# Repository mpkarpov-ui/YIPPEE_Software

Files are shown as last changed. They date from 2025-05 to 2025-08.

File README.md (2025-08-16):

# YIPPEE

**Your Integrated Presicion Positioning (and) Elevation Engine**

### About YIPPEE

YIPPEE is a personal project that I started in early 2025, and was my entry into hardware design, as I was interested in learning more about how my [college rocketry team](https://www.illinoisspacesociety.org/spaceshot) developed the hardware for its flight computers.

After receiving help from our Electronic Hardware lead, I had a schematic and layout I was happy with and produced it in our school's electronic lab. The software for this project was in majority written by me with some key contributions from [Surag Nuthulapaty](https://github.com/SuragNuthulapaty), who is a very smart and cool guy.

### Using YIPPEE

#### Hardware

All hardware schematics are present in `hardware/`. As of August 2025, the RPP diode is no longer being produced or sold, but can just be replaced with a jumper wire.

All components can be sourced commercially through Transfer Multisort Elektronik (TME), DigiKey, Mouser, LCSC, and Amazon.

All hardware schematics are free for use.

#### Software

YIPPEE software is compiled with [Platformio](https://platformio.org/), which offers easy VSCode integration with their extension. The configuration defines 4 targets which are described below:

**hardware_test** – This target suspends all normal functions of the flight computer and pre-empts them by putting in code configured to mass-test the components on the board, this is useful for board assembly and debugging.

**main** - This is the main "flight code" and includes finished drivers, flash memory management system, telemetry code, and a barometer-based flight FSM.

**mem_offload** – This target also pre-empts the main flight code, but instead of testing components, it allows offloading data off the flash memory chip.

**ground** (Feather M0) – Running on a commercial-off-the-shelf radio module (the Feather M0 RFM96), this code can receive YIPPEE radio signals and process them to display live board telemetry on the ground.

To start with your YIPPEE board, connect the USB port on the Teensy 4.0 to any COM port on your computer. Then flash the appropriate target through your Platformio interface of choice.

All YIPPEE software is free to reference.

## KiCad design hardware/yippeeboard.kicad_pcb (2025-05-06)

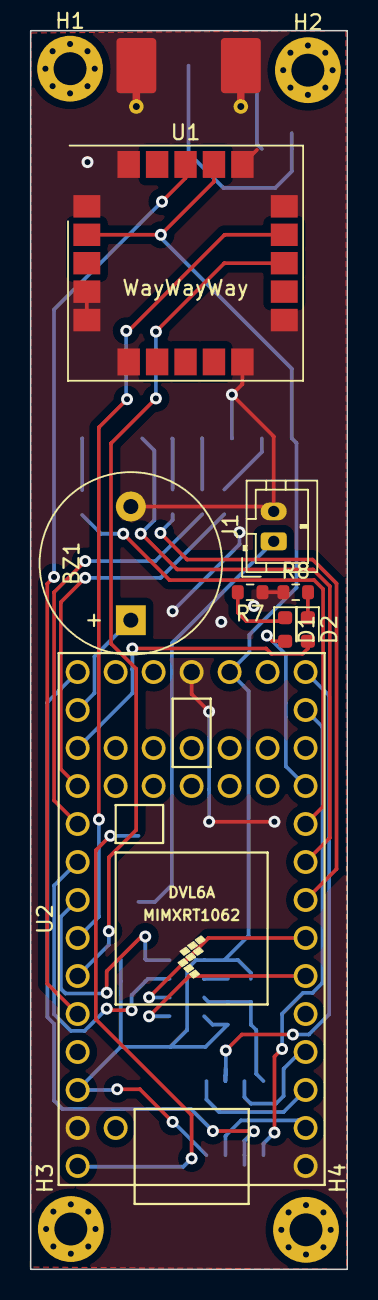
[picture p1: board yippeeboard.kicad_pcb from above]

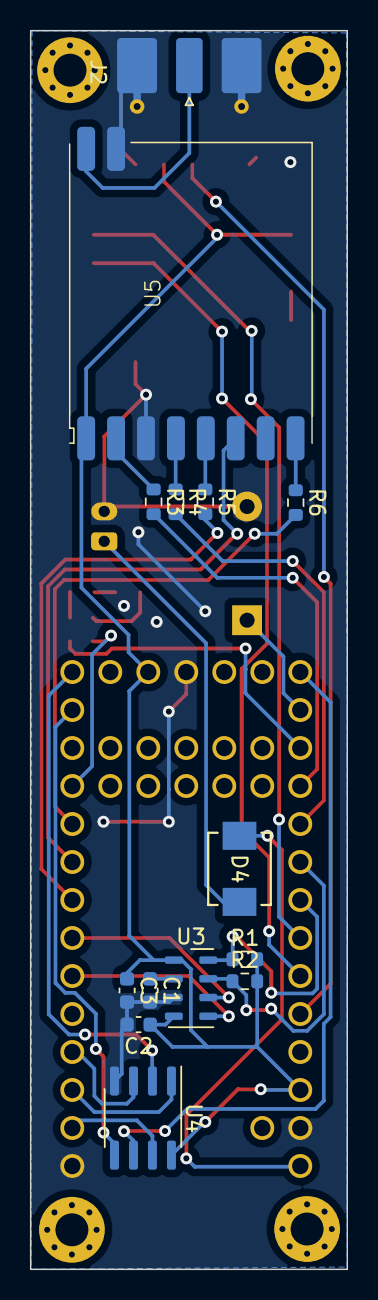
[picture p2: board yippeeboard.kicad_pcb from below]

Board: 2 copper layers, 21.2 x 82.8 mm, 26 parts (14 on the bottom side), 33 nets.

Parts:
BZ1: WST-1210; Buzzer_12x9.5RM7.6
C1, C3: 100 nF; C_0603_1608Metric
C2: 10 μF; C_0603_1608Metric
D1: LED_B; LED_0603_1608Metric
D2: LED_G; LED_0603_1608Metric
D4: LSM115JE3/TR13; DO-214BA_MCH
H1, H2, H3, H4: MountingHole_Pad; MountingHole_2.2mm_M2_Pad_Via
J1: Conn_01x02; JST_PH_B2B-PH-K_1x02_P2.00mm_Vertical
J2: Conn_Coaxial; SMA_Molex_73251-2120_EdgeMount_Horizontal
R1, R2: 4.7kΩ; R_0603_1608Metric
R3, R4, R5, R6: 22Ω; R_0603_1608Metric
R7, R8: 470; R_0603_1608Metric
U1: SAM-M10Q; ublox_SAM-M8Q
U2: Teensy4.0; Teensy40
U3: MPL3115A2; NXP_LGA-8_3x5mm_P1.25mm_H1.1mm
U4: SST26VF040A-104I/SN; SOIC-8_3.9x4.9mm_P1.27mm
U5: HM-TRLR-S-433; HM-TRLR-S-xxx

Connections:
+3V3: C2.1, C3.1, R1.2, R2.2, U1.2 (VCC_IO), U1.17 (VCC), U2.16 (3V3), U2.31 (3V3), U3.1 (VDD), U3.4 (VDDIO), U4.8 (VDD), U5.1 (VCC)
/BARO_INT1: U2.7 (5_IN2), U3.6 (INT1)
/BARO_INT2: U2.6 (4_BCLK2), U3.5 (INT2)
/BUZZER_SIG: BZ1.1 (-), U2.21 (14_A0_TX3_SPDIF_OUT)
/GPS_RESET: U1.18 (~RESET), U2.29 (22_A8_CTX1)
/GPS_RX: U1.13 (TXD), U2.28 (21_A7_RX5_BCLK1)
/GPS_TX: U1.14 (RXD), U2.27 (20_A6_TX5_LRCLK1)
/I2C_SCL: R1.1, U2.26 (19_A5_SCL0), U3.8 (SCL)
/I2C_SDA: R2.1, U2.25 (18_A4_SDA0), U3.7 (SDL)
/LED_B: D1.2 (A), U2.11 (9_OUT1C)
/LED_G: D2.2 (A), U2.22 (15_A1_RX3_SPDIF_IN)
/LORA_CONFIG: R5.2, U2.8 (6_OUT1D)
/LORA_RESET: R6.2, U2.10 (8_TX2_IN1)
/LORA_RX: R3.2, U2.23 (16_A2_RX4_SCL1)
/LORA_SLEEP: U2.9 (7_RX2_OUT1A), U5.6 (SLEEP)
/LORA_TX: R4.2, U2.24 (17_A3_TX4_SDA1)
/MEM_CS: U2.3 (1_TX1_CTX2_MISO1), U4.1 (~CE)
/MEM_HOLD: U2.2 (0_RX1_CRX2_CS1), U4.7 (~HOLD)
/MEM_WRITE_PROTECT: U2.4 (2_OUT2), U4.3 (~WP)
/PWR_VIN: D4.1 (K), U2.33 (VIN)
/SPI_MISO: U2.14 (12_MISO_MQSL), U4.2 (SO)
/SPI_MOSI: U2.13 (11_MOSI_CTX1), U4.5 (SI)
/SPI_SCK: U2.20 (13_SCK_CRX1_LED), U4.6 (SCK)
GND: BZ1.2 (+), C1.2, C2.2, C3.2, J1.2, J2.2 (Ext), R7.1, R8.1, U1.1 (GND), U1.4 (GND), U1.5 (GND), U1.6 (GND), U1.10 (GND), U1.11 (GND), U1.15 (GND), U1.16 (GND), U1.20 (GND), U2.1 (GND), U2.17 (GND), U2.32 (GND), U3.3 (GND), U4.4 (VSS), U5.3 (GND), U5.10 (GND)
unnamed: D1.1 (K), R7.2
unnamed: D2.1 (K), R8.2
unnamed: D4.2 (A), J1.1
unnamed: J2.1 (In), U5.9 (ANT)
unnamed: C1.1, U3.2 (CAP)
unnamed: R4.1, U5.4 (RXD)
unnamed: R3.1, U5.2 (TXD)
unnamed: R5.1, U5.5 (~CONFIG)
unnamed: R6.1, U5.8 (~RESET)

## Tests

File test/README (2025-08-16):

This directory is intended for PlatformIO Test Runner and project tests.

Unit Testing is a software testing method by which individual units of
source code, sets of one or more MCU program modules together with associated
control data, usage procedures, and operating procedures, are tested to
determine whether they are fit for use. Unit testing finds problems early
in the development cycle.

More information about PlatformIO Unit Testing:
- https://docs.platformio.org/en/latest/advanced/unit-testing/index.html

# This directory is unused for this project

## For tests, compile the hardware_test env on the board.

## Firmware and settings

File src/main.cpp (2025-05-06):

#include <Arduino.h>
#ifdef TEST_ENV
  #include <test_util.h>
#endif

#ifdef MEM_OFFLOAD
  #include <mem_offload/mem_offload.h>
#endif

#include "pins.h"
#include "buzzer.h"
#include "logger.h"
#include "HopeHM.h"
#include <Wire.h>
#include <MPL3115A2.h>
#include <SparkFun_u-blox_GNSS_v3.h>
#include <SST26VF040A.h>

// Check the config below to allow for booting with failures
// #define ALLOW_SETUP_FAILURES
// #define ENABLE_PROFILING

// 500ms / 2hz
#define LOG_FREQUENCY 500

// Threshold above pad that we detect launch
#define LAUNCH_THRESHOLD_ALT 20 // m
// Times we must read the launch threshold before we consider it a launch
#define CONSECUTIVE_LAUNCH_THRESHOLD 5

// At 50ms / 20hz, we need to read below the landing delta threshold for 3 seconds
#define CONSECUTIVE_LANDING_THRESHOLD 60 
#define LANDING_DELTA_THRESHOLD 5 // m

MPL3115A2 baro;
SFE_UBLOX_GNSS_SERIAL gps;
Logger mem(MEM_CS, MEM_HOLD, MEM_WRITE_PROTECT);
HopeHM lora(LORA_RESET, LORA_SLEEP, LORA_CONFIG);

struct board_data_t {
  bool init_no_err = true;

  // GPS
  bool gps_fix_ok = false;
  uint8_t gps_fix_type = 0;
  uint8_t gps_siv = 0;
  int32_t gps_latitude = 0;
  int32_t gps_longitude = 0;
  int32_t gps_altitude = 0;

  // Baro
  float baro_altitude = 0;
  float baro_temp = 0;
  float baro_pressure = 0;

  int32_t initial_baro_altitude = 0;

  // Flight data
  uint8_t FSM_state = 0; // 0=Preflight, 1=Flight, 2=Landed
  uint8_t flight_number = 0; // 0=F1, 1=F2
};

struct telem_t {
  // 1 if ok        1 if lock   0=F1, 1=F2      0=Preflight, 1=Flight    Channel 0-F       
  // INIT_NOERR   | GPS_LOCK? | CUR_FLIGHT_NO | FSM_STATE              | TELEM_CHANNEL(4bits) 
  uint8_t status;

  // GPS
  int32_t gps_latitude;
  int32_t gps_longitude;
  int32_t gps_altitude;
  int8_t gps_siv_fix_type; // 5 bits SIV, 3 bits fix type

  // Barometer
  float baro_altitude;
};

board_data_t global_data;
uint32_t NEXT_GPS_FLASH;
uint32_t NEXT_GPS_DATA;
uint32_t NEXT_TELEM_TRANSMIT;
uint32_t NEXT_LOGGER_COMMIT;
uint32_t NEXT_BAROMETER_READ;
uint32_t NEXT_LANDING_FLASH;
uint32_t CONSECUTIVE_BAROMETER_READS = 0;
uint32_t CONSECUTIVE_LANDING_READS = 0;
float LANDING_STATE_ALTITUDE = 0;
bool GPS_LIGHT_STATE = false;
bool TELE_LIGHT_STATE = false;
bool LAST_GPS_OK_STATE = false;

telem_t make_packet(const board_data_t& data) {
  char lora_channel = lora.get_channel();
  telem_t packet;
  packet.status = 0x00 & (lora_channel & 0x0F); // Mask out the channel bits
  packet.status |= (data.init_no_err & 0x01) << 7; // Set the init_no_err bit

  packet.gps_latitude = data.gps_latitude;
  packet.gps_longitude = data.gps_longitude;
  packet.gps_altitude = data.gps_altitude;
  packet.gps_siv_fix_type = (data.gps_siv << 3) | (data.gps_fix_type & 0x07); // SIV in upper bits, fix type in lower bits
  packet.baro_altitude = data.baro_altitude;
  return packet;
}

LoggerStruct make_logger_packet(const board_data_t& data) {
  LoggerStruct packet;
  packet.gps_altitude = data.gps_altitude;
  packet.baro_altitude = data.baro_altitude;
  packet.temp = data.baro_temp;
  packet.pres = data.baro_pressure;
  packet.timestamp = millis();
  packet.lat = data.gps_latitude;
  packet.lon = data.gps_longitude;
  packet.aux_data = ((data.FSM_state & 0x03) << 30) | ((data.gps_siv & 0x1F) << 25) | ((data.gps_fix_type & 0x07) << 22) | ((data.flight_number & 0x01) << 21) | (lora.get_channel() & 0x0F) << 17;
  return packet;
}

board_data_t decode_packet(uint8_t* data, size_t len) {
  board_data_t packet;
  if(len != sizeof(telem_t)) {
    return packet; // Invalid packet size
  }
  telem_t* telem = (telem_t*)data;
  packet.gps_latitude = telem->gps_latitude;
  packet.gps_longitude = telem->gps_longitude;
  packet.gps_altitude = telem->gps_altitude;
  packet.gps_siv = (telem->gps_siv_fix_type >> 3) & 0x1F; // Extract SIV from upper bits
  packet.gps_fix_type = telem->gps_siv_fix_type & 0x07; // Extract fix type from lower bits
  return packet;
}

bool transmit_telemetry() {
  telem_t packet = make_packet(global_data);
  size_t packet_size = sizeof(packet);
  uint8_t* packet_data = (uint8_t*)&packet;

  return lora.transmit(packet_data, packet_size);
}

void setup() {
  #ifdef TEST_ENV
    // Run test setup
    YIPPEE_TEST_SETUP();
    return;
  #endif

  #ifdef MEM_OFFLOAD
    // Run memory offload setup
    YIPPEE_MEM_OFFLOAD_SETUP(&mem);
    return;
  #endif
  
  // Set up all pins
  pinMode(BUZZER, OUTPUT);
  pinMode(LED_BLUE, OUTPUT);
  pinMode(LED_GREEN, OUTPUT);
  pinMode(MEM_CS, OUTPUT);
  pinMode(MEM_HOLD, OUTPUT);
  pinMode(MEM_WRITE_PROTECT, OUTPUT);
  pinMode(LORA_RESET, OUTPUT);
  pinMode(LORA_SLEEP, OUTPUT);
  pinMode(LORA_CONFIG, OUTPUT);

  // Show signs of life!
  digitalWrite(LED_BLUE, HIGH);
  BUZZ_INIT();
  digitalWrite(LED_BLUE, LOW);


  // Init all interfaces
  Serial5.begin(9600);
  Serial4.begin(9600);
  Serial.begin(9600);
  SPI.begin();
  Wire.begin();

  NEXT_GPS_FLASH = millis() + 500;
  NEXT_TELEM_TRANSMIT = millis();
  NEXT_GPS_DATA = millis();
  NEXT_LOGGER_COMMIT = millis();
  NEXT_BAROMETER_READ = millis();

  // Try to init GPS 
  bool gps_has_init = gps.begin(Serial5);
  
  gps.setDynamicModel(DYN_MODEL_AIRBORNE4g);
  gps.setAutoNAVSAT(true);
  gps.setAutoPVT(true);

  if(!gps_has_init) { global_data.init_no_err = false; }
  #ifndef ALLOW_SETUP_FAILURES
    // Fail loudly.
    if(!gps_has_init) {
      Serial.println("Failed to init GPS!");
      digitalWrite(LED_GREEN, HIGH); // Flashing green LED = GPS fail
      BUZZ_FAIL_GPS();

      while(1) {
        digitalWrite(LED_GREEN, HIGH);
        delay(50);
        digitalWrite(LED_GREEN, LOW);
        delay(50);
      };
    }
  #endif



  // Flash init
  digitalWrite(MEM_HOLD, HIGH);
  digitalWrite(MEM_WRITE_PROTECT, HIGH);

  bool flash_init_stat = mem.begin();
  if(!flash_init_stat) { global_data.init_no_err = false; }
  #ifndef ALLOW_SETUP_FAILURES
    // Fail loudly.
    if(!flash_init_stat) {
      Serial.println("Failed to init Flash!");
      digitalWrite(LED_BLUE, HIGH); // Flashing blue is flash failure
      BUZZ_FAIL_MEM();

      while(1) {
        digitalWrite(LED_BLUE, HIGH);
        delay(50);
        digitalWrite(LED_BLUE, LOW);
        delay(50);
      };
    }
  #endif

  // Baro init
  baro.begin(Wire, 0x60);
  baro.setModeAltimeter();
  baro.setOversampleRate(5);
  baro.enableEventFlags();

  // Lora init
  Serial.println("Initing lora..");
  bool lora_init_stat = lora.begin(&Serial4);

  lora.begin_config();
  lora_init_stat &= lora.set_tx_power(HOPEHM_TX_POWER::TX_POWER_20DB);
  lora_init_stat &= lora.set_channel(HOPEHM_CHANNEL::CHANNEL_0);
  lora_init_stat &= lora.set_enable_crc(true);
  lora_init_stat &= lora.set_lora_bandwidth(HOPEHM_BANDWIDTH::BW_125KHZ);
  lora_init_stat &= lora.set_lora_spreading_factor(HOPEHM_SPREADINGFACTOR::SF_7);
  lora_init_stat &= lora.set_lora_codingrate4(HOPEHM_CODINGRATE4::CR_4_5);

  lora.end_config();
  #ifndef ALLOW_SETUP_FAILURES
    // Fail loudly.
    if(!lora_init_stat) {
      Serial.println("Failed to init LoRa!");
      digitalWrite(LED_BLUE, HIGH); // Both LEDs flashing is lora failure
      BUZZ_FAIL_LORA();

      while(1) {
        digitalWrite(LED_BLUE, HIGH);
        digitalWrite(LED_GREEN, LOW);
        delay(50);
        digitalWrite(LED_BLUE, LOW);
        digitalWrite(LED_GREEN, HIGH);
        delay(50);
      };
    }
  #endif

  // Show setup finished! (And play YIPPEE tone!)
  BUZZ_YIPPEE();
}

void get_gps_data() {
  global_data.gps_fix_ok = gps.getGnssFixOk(50);
  global_data.gps_siv = gps.getSIV(50);

  if(global_data.gps_siv > 100) {
    global_data.gps_siv = 0;
  }
  if(global_data.gps_fix_ok) {
    global_data.gps_fix_type = gps.getFixType(50);
    global_data.gps_latitude = gps.getLatitude(50);
    global_data.gps_longitude = gps.getLongitude(50);
    global_data.gps_altitude = gps.getAltitude(50);
  }
}

void DEBUG_print_gps_data() {
  Serial.println("== DEBUG: GPS ==");
  Serial.print("(FIX OK / SIV):  ");
  Serial.print(global_data.gps_fix_ok);
  Serial.print(" / ");
  Serial.println(global_data.gps_siv);

  if(global_data.gps_fix_ok) {
    Serial.println("GPS FIX OK!");
    Serial.print("FT: ");
    Serial.println(global_data.gps_fix_type);
    Serial.print("(LAT/LON/ALT): ");
    Serial.print(global_data.gps_latitude);
    Serial.print(" / ");
    Serial.print(global_data.gps_longitude);
    Serial.print(" / ");
    Serial.println(global_data.gps_altitude);
  } else {
    Serial.println("NO FIX");
  }
}

void loop() {
  #ifdef TEST_ENV
    // Run test loop and ignore other code.
    YIPPEE_TEST_LOOP();
    return;
  #endif

  #ifdef MEM_OFFLOAD
    // Run memory offload loop and ignore other code.
    YIPPEE_MEM_OFFLOAD_LOOP(&mem);
    return;
  #endif

  #ifdef ENABLE_PROFILING
    uint32_t CUR_PROC_TIME = millis();
  #endif
  
   // We will only attempt getting GPS data every 500ms
  if(millis() > NEXT_GPS_DATA) {
    #ifdef ENABLE_PROFILING
      Serial.print("[PROFILER] GPS ... ");
      CUR_PROC_TIME = millis();
    #endif
    NEXT_GPS_DATA = millis() + 100;
    get_gps_data();
    DEBUG_print_gps_data();
    #ifdef ENABLE_PROFILING
      CUR_PROC_TIME = millis() - CUR_PROC_TIME;
      Serial.println("Done! (" + String(CUR_PROC_TIME) + "ms)");
    #endif
  }
  
  if(global_data.gps_fix_ok) {
    if(LAST_GPS_OK_STATE == false) {
      LAST_GPS_OK_STATE = true;
      // Lil beeps to tell us gps is ok!
      BUZZ_GPS_LOCK_ACQUIRED();
      GPS_LIGHT_STATE = true;
      digitalWrite(LED_GREEN, HIGH);
    }

  } else {
    if(LAST_GPS_OK_STATE == true) {
      // We lost lock :(
      LAST_GPS_OK_STATE = false;
      GPS_LIGHT_STATE = false;
      digitalWrite(LED_GREEN, LOW);

      BUZZ_GPS_LOCK_LOST();
      
    }
    if(millis() > NEXT_GPS_FLASH) {
      if(global_data.gps_siv > 0) {
        Serial.println("Satellites are in view.. attempting to acquire lock");
        NEXT_GPS_FLASH = millis() + 350;
        GPS_LIGHT_STATE = !GPS_LIGHT_STATE;
        digitalWrite(LED_GREEN, GPS_LIGHT_STATE ? HIGH : LOW);
        BUZZ_GPS_SAT_IN_VIEW();
      } else {
        NEXT_GPS_FLASH = millis() + 750;
        GPS_LIGHT_STATE = !GPS_LIGHT_STATE;
        digitalWrite(LED_GREEN, GPS_LIGHT_STATE ? HIGH : LOW);
      }
    }
  }

  // Transmit telemetry data
  if(millis() > NEXT_TELEM_TRANSMIT && lora.has_init_succeeded()) {
    #ifdef ENABLE_PROFILING
      Serial.print("[PROFILER] TELEMETRY ... ");
      CUR_PROC_TIME = millis();
    #endif
    if(transmit_telemetry()) {
      TELE_LIGHT_STATE = !TELE_LIGHT_STATE;
      digitalWrite(LED_BLUE, TELE_LIGHT_STATE ? HIGH : LOW);
    } else {
      BUZZ_FAIL_TRANSMIT();
    }
    #ifdef ENABLE_PROFILING
      CUR_PROC_TIME = millis() - CUR_PROC_TIME;
      Serial.println("Done! (" + String(CUR_PROC_TIME) + "ms)");
    #endif
    NEXT_TELEM_TRANSMIT = millis() + 500;
  }

  // Log data to flash memory
  if(millis() > NEXT_LOGGER_COMMIT) {
    #ifdef ENABLE_PROFILING
      Serial.print("[PROFILER] LOGGING ... ");
      CUR_PROC_TIME = millis();
    #endif
    LoggerStruct packet = make_logger_packet(global_data);
    mem.write(packet);
    NEXT_LOGGER_COMMIT = millis() + LOG_FREQUENCY;
    #ifdef ENABLE_PROFILING
      CUR_PROC_TIME = millis() - CUR_PROC_TIME;
      Serial.println("Done! (" + String(CUR_PROC_TIME) + "ms)");
    #endif
  }

  if(millis() > NEXT_BAROMETER_READ) {
    #ifdef ENABLE_PROFILING
      Serial.print("[PROFILER] BARO ... ");
      CUR_PROC_TIME = millis();
    #endif

    global_data.baro_altitude = baro.readAltitude();
    global_data.baro_temp = baro.readTemp();
    global_data.baro_pressure = baro.readPressure();


    if(global_data.initial_baro_altitude == 0) {
      global_data.initial_baro_altitude = global_data.baro_altitude;

    } else {
      // Check if we are above the launch threshold
      int32_t delta_altitude = global_data.baro_altitude - global_data.initial_baro_altitude;

      if(delta_altitude < LAUNCH_THRESHOLD_ALT) {
        CONSECUTIVE_BAROMETER_READS = 0;
      } else {
        CONSECUTIVE_BAROMETER_READS++;
      }
  
      if(CONSECUTIVE_BAROMETER_READS >= CONSECUTIVE_LAUNCH_THRESHOLD && global_data.FSM_state == 0) {
        // We have launched! Set FSM state to 1 (Transition)
        Serial.println("LAUNCH DETECTED!");
        global_data.FSM_state = 1;
        mem.change_state(global_data.FSM_state);
        BUZZ_YIPPEE_LAUNCH();
      }

      if(global_data.FSM_state == 1) {
        
        if(abs(global_data.baro_altitude - LANDING_STATE_ALTITUDE) < LANDING_DELTA_THRESHOLD) {
          CONSECUTIVE_LANDING_READS++;
        } else {
          CONSECUTIVE_LANDING_READS = 0;
          LANDING_STATE_ALTITUDE = global_data.baro_altitude;
        }

        if(CONSECUTIVE_LANDING_READS >= CONSECUTIVE_LANDING_THRESHOLD) {
          // We have landed! Set FSM state to 2 (Landed)
          Serial.println("LANDING DETECTED!");
          global_data.FSM_state = 2;
          mem.change_state(global_data.FSM_state);
        }
      }
    }

    if(millis() > NEXT_LANDING_FLASH && global_data.FSM_state == 2) {
      // Flash the blue LED to indicate we are in flight
      BUZZ_YIPPEE_LANDING();
      NEXT_LANDING_FLASH = millis() + 1500;
    }
    

    NEXT_BAROMETER_READ = millis() + 50;
    #ifdef ENABLE_PROFILING
      CUR_PROC_TIME = millis() - CUR_PROC_TIME;
      Serial.println("Done! (" + String(CUR_PROC_TIME) + "ms)");
    #endif
  }

  delay(1);
}

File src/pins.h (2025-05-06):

#pragma once
// Defines all MCU pins

#define LED_BLUE 9
#define LED_GREEN 15

#define I2C_SDA 18
#define I2C_SCL 19

#define GPS_TX 20
#define GPS_RX 21
#define GPS_RESET 22

#define LORA_TX 17
#define LORA_RX 16
#define LORA_RESET 8
#define LORA_SLEEP 7
#define LORA_CONFIG 6

#define BUZZER 14

#define SCK 13
#define MISO 12
#define MOSI 11

#define MPL311_INT_1 5
#define MPL311_INT_2 4
#define MPL311_ADDR 0x60

#define MEM_WRITE_PROTECT 2
#define MEM_CS 1
#define MEM_HOLD 0

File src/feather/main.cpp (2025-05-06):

#include <RH_RF95.h>
#include <SPI.h>

#include <array>
#include <limits>
#include <numeric>
#include <queue>
#include <algorithm>

#include "SerialParser.h"

/* Pins for feather*/
// // Ensure to change depending on wiring
#define RFM95_CS 8
#define RFM95_RST 4
// #define RFM95_EN
#define RFM95_INT 3
#define VoltagePin 14
// #define LED 13 // Blinks on receipt


float RF95_FREQ = 430.00;
float rf95_freq_MHZ = RF95_FREQ;

float current_freq = 0;


struct telem_t {
    // 1 if ok        1 if lock   0=F1, 1=F2      0=Preflight, 1=Flight    Channel 0-F       
    // INIT_NOERR   | GPS_LOCK? | CUR_FLIGHT_NO | FSM_STATE              | TELEM_CHANNEL(4bits) 
    uint8_t status;
  
    // GPS
    int32_t gps_latitude;
    int32_t gps_longitude;
    int32_t gps_altitude;
    int8_t gps_siv_fix_type; // 5 bits SIV, 3 bits fix type
  
    // Barometer
    float baro_altitude;
  };

typedef uint32_t systime_t;
// Singleton instance of the radio driver
RH_RF95 rf95(RFM95_CS, RFM95_INT);
// For reading from

void setup() {
    while (!Serial)
        ;
    Serial.begin(9600);
    if (!rf95.init()) {
        Serial.println("Failed to init");
        while (1);
    }
    pinMode(LED_BUILTIN, OUTPUT);
    Serial.println("Yippee!");
    if (!rf95.setFrequency(rf95_freq_MHZ)) {
        Serial.println("Failed to set freq");
        while (1);
    }
    
    current_freq = rf95_freq_MHZ;

    rf95.setCodingRate4(5);
    rf95.setSpreadingFactor(7);

    rf95.setPayloadCRC(true);

    rf95.setSignalBandwidth(125000);
    // rf95.setPreambleLength(10);

    Serial.print(R"({"type": "freq_success", "frequency":)");
    Serial.print(current_freq);
    Serial.println("}");
    rf95.setTxPower(23, false);

    Serial.setTimeout(250);
}

// void ChangeFrequency(float freq) {
//     float current_time = millis();
//     rf95.setFrequency(freq);
//     Serial.println(json_command_success);
//     Serial.print(R"({"type": "freq_success", "frequency":)");
//     Serial.print(freq);
//     Serial.println("}");
// }


void loop() {

    if (rf95.available()) {
        uint8_t buf[RH_RF95_MAX_MESSAGE_LEN];
        uint8_t len = sizeof(telem_t);
        telem_t data;

        if (rf95.recv(buf, &len)) {
            digitalWrite(LED_BUILTIN, HIGH);
            delay(50);
            digitalWrite(LED_BUILTIN, LOW);

            memcpy(&data, buf, len);

            // Serial.println("Fresh packet: ");

            // Decode all the data!

            bool init_noerr = (data.status & (1<<7)) >> 7; // init_noerr is the top bit
            bool gps_locked = (data.status & (1<<6)) >> 6;
            uint8_t fsm_state = (data.status & (0x3 << 4)) >> 4;
            uint8_t telem_chan = (data.status & 0xF);

            char* fsm_state_str = "PREFLIGHT";
            if(fsm_state == 1) {
                fsm_state_str = "FLIGHT";
            }

            if(fsm_state == 2) {
                fsm_state_str = "LANDED";
            }


            uint8_t siv = (data.gps_siv_fix_type & 0xF8) >> 3;
            uint8_t fix_type = data.gps_siv_fix_type & 0x7;
            Serial.print(telem_chan);
            Serial.print(init_noerr ? " OK " : " ERR ");
            Serial.print(fsm_state_str);
            Serial.print(gps_locked ? " LOCKED (" : " NOLOCK (");
            Serial.print(data.gps_latitude);
            Serial.print(" / ");
            Serial.print(data.gps_longitude);
            Serial.print(" / ");
            Serial.print(data.gps_altitude);
            Serial.print(") SIV ");
            Serial.print(siv);
            Serial.print(" FXT ");
            Serial.print(fix_type);
            Serial.print(" BARO ");
            Serial.print(data.baro_altitude, 2);
            Serial.print(" RSSI ");
            Serial.println(rf95.lastRssi());
            

            // // print out buf

            // for(unsigned i = 0; i < len; i++) {
            //     Serial.print(buf[i]);
            // }

            // Serial.println("   <eot>");

        } else {
            Serial.println(Serial.println("Failed to recieve"));
        }
    }

}

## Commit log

2025-04-30 potential flash driver
2025-04-30 full flow ?
2025-05-02 mem offload
    [hello0.csv, hello1.csv, opel_test.csv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]
2025-05-06 more stuff
    [hello0.csv, hello1.csv, opel_test.csv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]
2025-05-06 add hardware
    [yippeeboard.kicad_pcb, yippeeboard.kicad_sch]
